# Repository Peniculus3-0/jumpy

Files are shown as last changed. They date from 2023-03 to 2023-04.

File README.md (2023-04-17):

# Jumpy

Jumpy est un robot sauteur réalisé dans le cadre du projet de session de la session 4 en Génie Robotique à l'Université de Sherbrooke. 

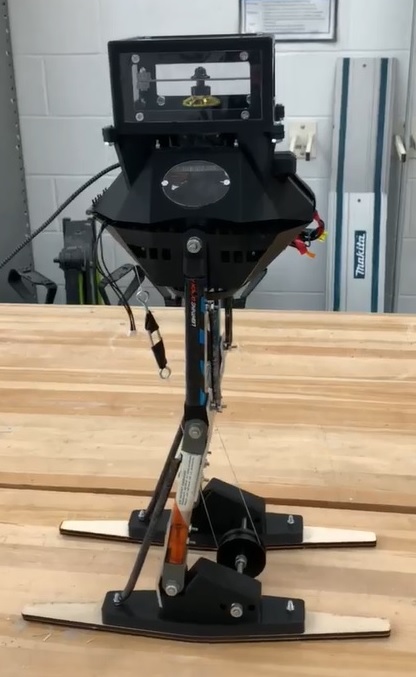
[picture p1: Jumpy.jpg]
JUMPY


## Table des matières

* [UI](/UI#requis)
* [Code contrôle](/Code/mainJumpy#code)
* [CAD](/CAD#CAD)

## VIDÉOS

[Démonstration du robot](https://www.youtube.com/shorts/cel7XVDD8pQ)

[Démonstration du saut à une jambe](https://www.youtube.com/shorts/icxFYxDteIQ)

[Démonstration de la roue inertielle](https://www.youtube.com/shorts/jROJLMc7-dI)

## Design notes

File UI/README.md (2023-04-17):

### Fonctionnalités

- Affichage de l'interface utilisateur avec un thème clair, sombre ou système.
- Recherche de dispositifs Bluetooth à proximité à l'aide du module bleak.
- Connexion à un dispositif Bluetooth sélectionné dans une liste déroulante.
- Animation du robot qui saute
- Lance le saut à distance par Bluetooth
- Affichage en temps réel de la vitesse et du couple actuels du moteur.

### Requis

1. Un ordinateur avec Python 3.x installé.
2. Un dispositif Bluetooth compatible pour contrôler le moteur.
3. Les modules Python suivants installés : customtkinter, PIL (Pillow), bleak, threading, os, logging, asyncio et turtle.
4. Lien vers les images des animations : https://drive.google.com/drive/folders/1fHX3-iR9xY-f3sybb7qTc169rCVtT3Wu?usp=sharing

  `pip install requirements.txt`
  
  ### Procédure
  
1. Assurez-vous que tous les prérequis sont satisfaits.
3. Exécutez le fichier UI.py pour lancer l'application.
4. L'application affichera l'interface utilisateur avec les options de recherche de dispositifs Bluetooth.
5. Sélectionnez un dispositif Bluetooth dans la liste déroulante et connectez-vous.

  ### Classe animation
  
- Affiche l'animation de repos et de saut du robot dans un frame custom Tkinter à une fréquence spécifié en bouclant les images en mémoire
- Charge les images dans des dictionnaires pour améliorer les performances

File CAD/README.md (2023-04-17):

# CAD
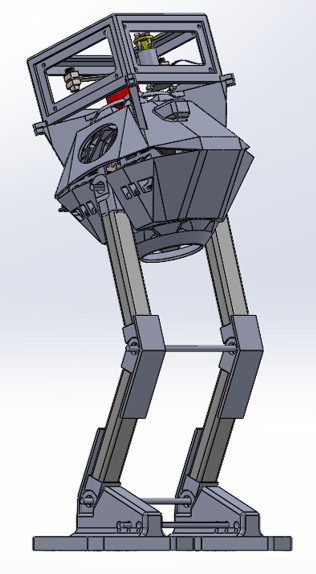
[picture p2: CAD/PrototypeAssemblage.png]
Assemblage

## REQUIS
* Une imprimante 3D
* Pour le reste des pièces, voir le [BOM](/BOM.pdf)

## PROCÉDURE

1. Imprimer les pièces 3D
2. Découper les plaques d'acrylique au laser
3. Découper et percer les plaques d'acier
4. Découper et plier les plaques d'aluminium
5. Couper les bâtons de hockey
6. Assembler les pièces imprimées et les bâtons

## ASSEMBLAGE DU ROBOT

### JAMBE

##### PIÈCES À IMPRIMER:
- Pied_V4_ECP (x2)
- Cheville_REV2_VF (x2)
- PoulieCheville_V1_CN (x1)
- JointDouble_REV0_AM (x6)

### BOITE DE CONTROLE

##### PIÈCES À IMPRIMER:
- AcrylicCage_V1_CN (x1)
- ControlBoxFrame_V2_CN (x1)
- TopFrame_V1_CN_InProgress (x1)
- GearMoteur_V5_ECP (x2)
- GearPulleyV1_LC (x1)
- Hinge_REV0_LC (x3)
- MotorHolder_V1_LCV (x1)

##### PLAQUES D'ACRYLIQUE À DÉCOUPER:
- AcrylicPlaqueSide1_V1_CN (x4)
- AcrylicPlaqueTop_V1_CN (x1)
- AcrylicWindowTopFrame_V1_CN (x1)

### ROUE INERTIELLE

##### PLAQUES D'ALUMINIUM À DÉCOUPER ET PLIER:
- Stopper20deg_REV0_CL (x2)
- Stopper40deg_REV0_CL (x2)

##### PLAQUES D'ACIER À DÉCOUPER ET PERCER
- PlaqueEpaisseFlywheel_CN_V2 (x4)
- PlaqueMinceFlywheel_CN_V2 (x1)

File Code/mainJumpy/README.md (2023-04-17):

# Code
## Installation OpenCR via le gestionnaire de cartes : 

1.	Une fois l'IDE Arduino exécuté, cliquez sur Fichier → Préférences dans le menu supérieur de l'IDE. Lorsque la fenêtre Préférences apparaît, copiez et collez le lien suivant dans la zone de texte URL supplémentaires du gestionnaire de cartes. (Cette étape peut prendre environ 20 minutes.)

https://raw.githubusercontent.com/ROBOTIS-GIT/OpenCR/master/arduino/opencr_release/package_opencr_index.json

2.	Cliquez sur Outils → Tableau → Gestionnaire de carte.
3.	Tapez OpenCR dans la zone de texte pour trouver le package OpenCR by ROBOTIS. Une fois trouvé, cliquez sur Installer.
4.	Après l'installation, "INSTALLÉ" apparaîtra.
5.	Vérifiez si la carte OpenCR est maintenant dans la liste Outils → Carte. Cliquez dessus pour importer la source de la carte OpenCR.

### Pour plus d’information :
https://emanual.robotis.com/docs/en/parts/controller/opencr10/#install-on-windows

## Installation des librairies :

1.	Cliquez sur Croquis → Inclure une bibliothèque → Gérer les bibliothèques.
2.	Tapez Dynamixel2Arduino dans la zone de texte pour trouver la bibliothèque by ROBOTIS. Une fois trouvé, cliquez sur Installer.
3.	Après l'installation, "INSTALLÉ" apparaîtra.

### Pour plus d’information :
https://docs.arduino.cc/software/ide-v1/tutorials/installing-libraries

## Utilisation du code Arduino :

Il n’y a que trois commandes possibles pour utiliser le code à partir du moniteur série :
-	« j » pour sauter sans tourner.
-	« l » pour sauter et tourner vers la gauche.
-	« r » pour sauter et tourner vers la droite. 
L’instruction « w » est juste un état qui ne fais rien en attendant la prochaine instruction.

Une fois qu’un saut est initié, il y a trois façons possibles de terminer une boucle de saut :
-	Le saut est détecté par une baisse soudaine de courant.
-	L’arrêt d’urgence est activé à cause d’un courant trop élevé
-	L’arrêt manuel est activé en envoyant n’importe quel caractère dans le moniteur série.

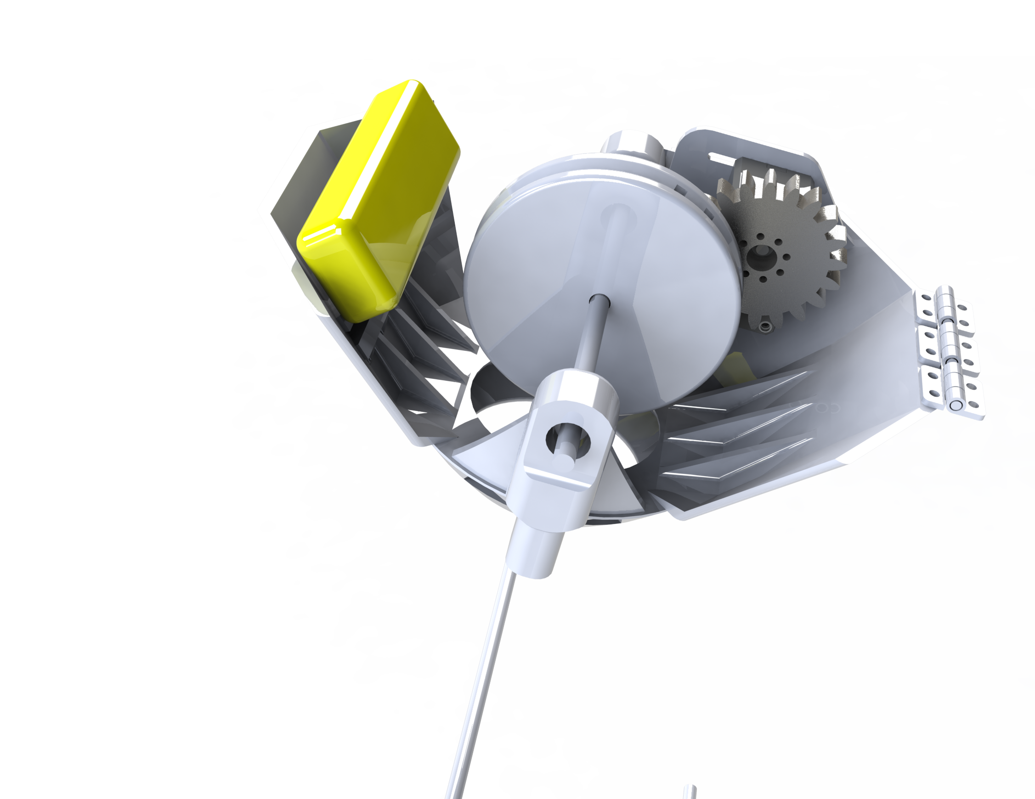
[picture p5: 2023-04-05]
UI/images/robot.png

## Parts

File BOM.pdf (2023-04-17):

Tableau 1 : Liste des pièces mécaniques du projet

Pièce | Description | Emplacement sur le
robot | Coût unitaire Fournisseur | Quantité | Coût total
1kg de PLA | - | - | 25 | FILAMENTS.CA | 1 | 25
Bâton de hockey | 20 cm | Jambes | 118.99 | Sports experts | 1 | 118.99
Ressorts | 800 N/m – 12 cm | Jambes | 5.95 | McMaster-Carr | 2 | 11.90
Ressorts | 800 N/m – 19 cm | Jambes | 5.95 | McMaster-Carr | 2 | 11.90
Roulements à bille | 10pcs Kozelo FR188ZZ Jambes | 19.49 | Amazon | 2 | 38.98
Arbre | ¼"φ – 20 cm | Jambes | 6.75 | McMaster-Carr | 3 | 19.50
Bague | 10pcs ¼"φ | Jambes | 18.74 | Amazon | 2 | 37.58
M3 boulons & noix | 100pcs – 20mm | Jambes & boîte contrôle | 4.99 | Amazon | 1 | 4.99
M4 boulons & noix | 100pcs – 20mm | Jambes & boîte contrôle | 4.99 | Amazon | 1 | 4.99
M5 boulons & noix | 100pcs – 20mm | Jambes & boîte contrôle | 4.99 | Amazon | 1 | 4.99
TOTAL | | | | | | 278.82

Tableau 2 : Liste des pièces électriques du projet

Grand total : 1300.14 CAD

Pièce | Description | Emplacement sur le
robot | Coût unitaire Fournisseur | Quantité | Coût total
Carte OpenCR | - | Boîte de contrôle supérieure 250 | Projet S4-GRO | 1 | 250
Dynamixel XM430 | - | Boîte de contrôle inférieure 300 | Projet S4-GRO | 2 | 600
Batterie Lithium | 3S – 25C | Boîte de contrôle inférieure 28.99 | AlieExpress | 1 | 28.99
Moteur BLDC | Scorpion M-3011-
760kv | Boîte de contrôle supérieure 89.99 | ScorpionSystem | 1 | 89.99
Contrôleur de vitesse ESC 25A | Boîte de contrôle supérieure 25.99 | ScorpionSystem | 1 | 25.99
Module bluetooth | DSD TECH HM-10 | Boîte de contrôle supérieure 14.39 | Amazon | 1 | 14.39
Fusible 5A | Fusible temporisé lent Boîte de contrôle supérieure 0.49 | Amazon | 1 | 0.49
Fusible 20A | Fusible temporisé lent Boîte de contrôle supérieure 0.49 | Amazon | 1 | 0.49
Fil | 18 AWG – 20 pieds | Boîte de contrôle | 10.98 | Amazon | 1 | 10.98
TOTAL | | | | | | 1021.32

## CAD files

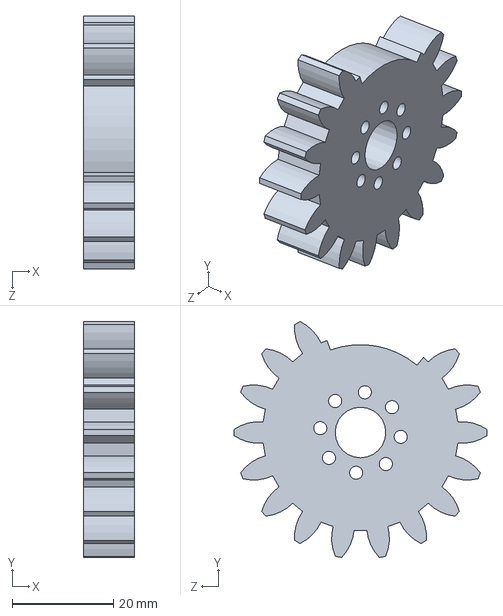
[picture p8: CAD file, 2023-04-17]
CAD/GearMoteur_V5_ECP.SLDASM
10.0 x 46.7 x 50.0 mm

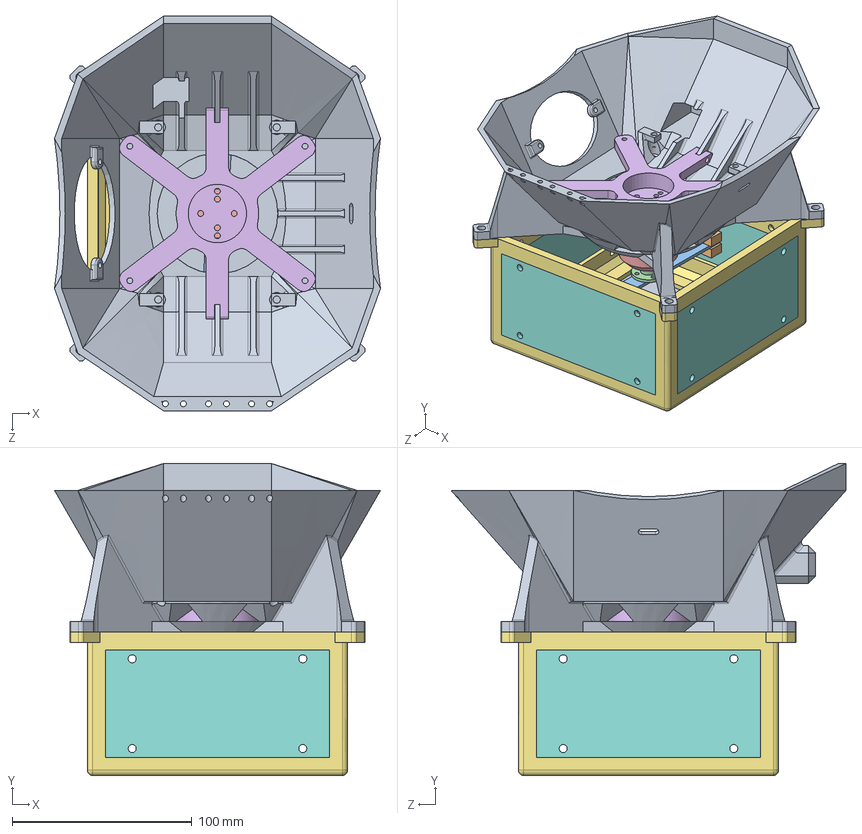
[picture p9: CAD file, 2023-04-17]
CAD/TopFrameWithFlywheel_V1_CN.SLDASM
181.6 x 173.8 x 220.0 mm
TopFrame_V1_CN_InProgress
PlaqueEpaisseFlywheel_CN_V2 x 4
PlaqueMinceFlywheel_CN_V2
FlywheelFlangeCoupling_V1_LC
FlywheelMotor_LCV_V2.smg
MotorHolder_V1_LCV
AcrylicCage_V1_CN
AcrylicPlaqueSide1_V1_CN x 4
AcrylicPlaqueTop_V1_CN

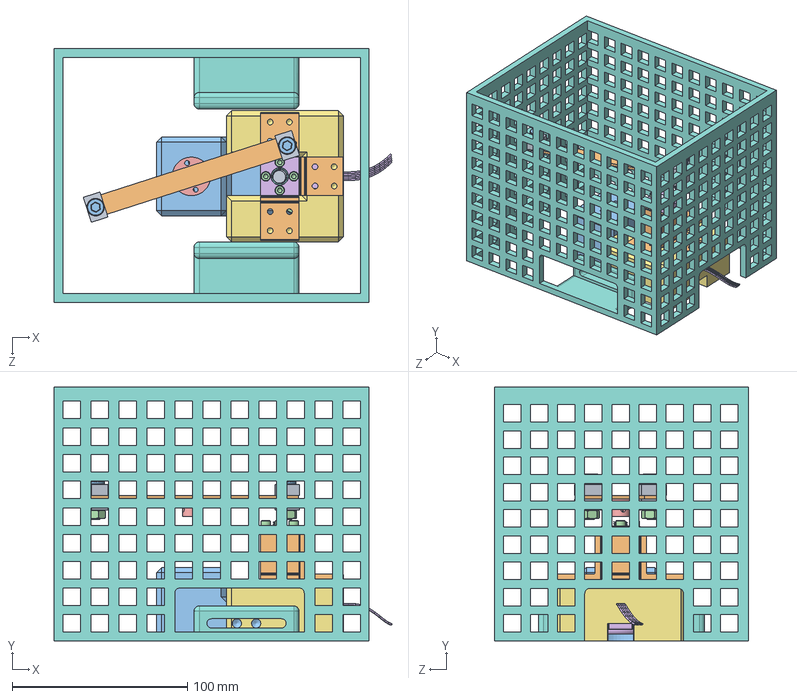
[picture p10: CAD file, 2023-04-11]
SherwoodUpToDate/FlywheelExternPrototype_V1_LC.SLDASM
193.1 x 145.0 x 145.0 mm
PlaqueEpaisseFlywheel_CN_V2 x 4
PlaqueMinceFlywheel_CN_V2
GB_1 x 2
M6 Hex nut x 2
FlywheelFlangeCoupling_V1_LC
Stepper motor 1PC.stp
LeadScrewMotorCoupler_V1_LC
LeadScrewNut_V1_LC
LeadScrew_V1_LC
AluminumSideBlocker_V1_LC x 3
FlywheelBrakePrototypeFrame_V1_LC
socket head cap screw_am x 6
hex nut style 1_am x 6
AluminumShaftStopper_V1_LC x 3
FlywheelTopFrame_V1_LC
CageFlywheel_V1_CN

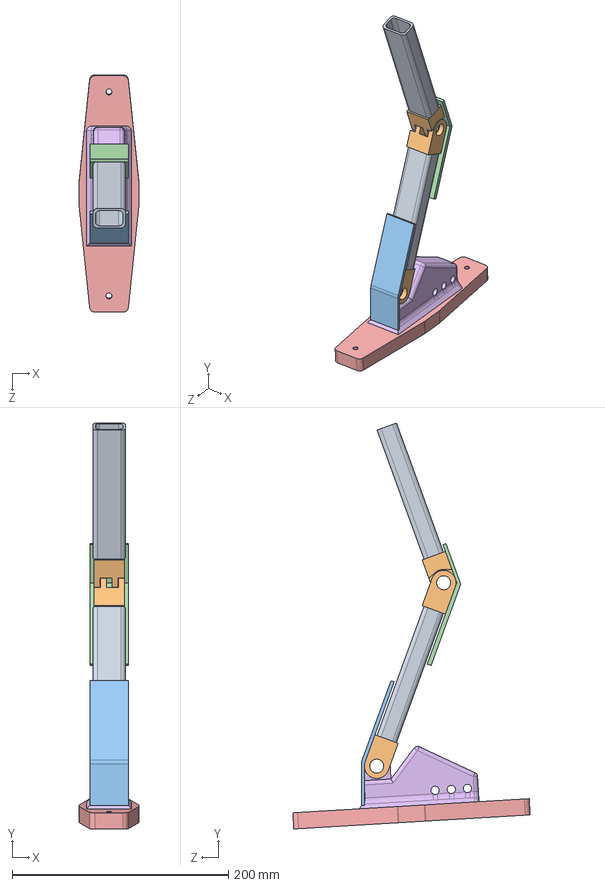
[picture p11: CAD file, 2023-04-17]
CAD/AssemblageJambe_REV3_CL.SLDASM
55.0 x 375.2 x 219.5 mm
Membre_REV0_CL x 2
JointDouble_REV0_AM x 3
Stopper20deg_REV0_CL
Stopper40deg_REV0_CL
Pied_V4_ECP.step
Cheville_REV2_VF

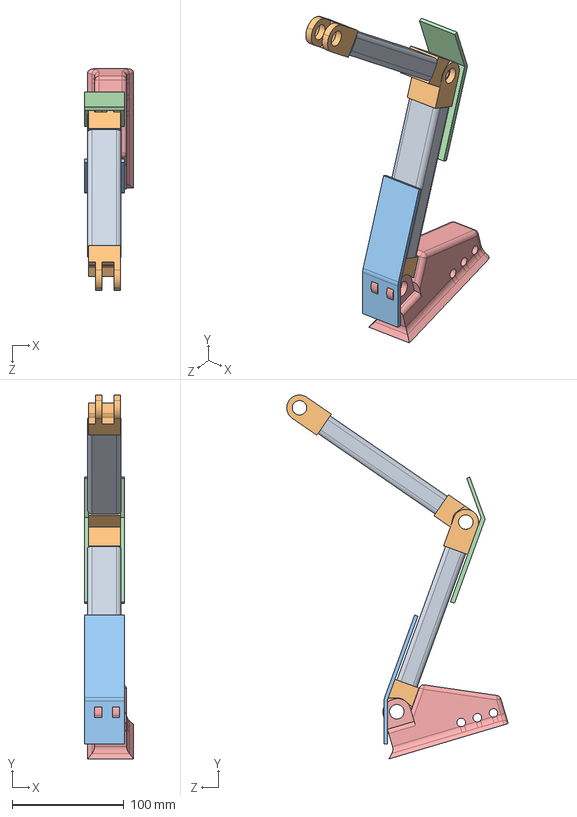
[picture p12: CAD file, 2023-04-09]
SherwoodUpToDate/AssemblageJambe_REV4_ECP.SLDASM
44.2 x 325.3 x 198.0 mm
Membre_REV0_CL x 2
JointDouble_REV0_AM x 4
Stopper20deg_REV0_CL
Stopper40deg_REV0_CL
Cheville_REV1_ECP

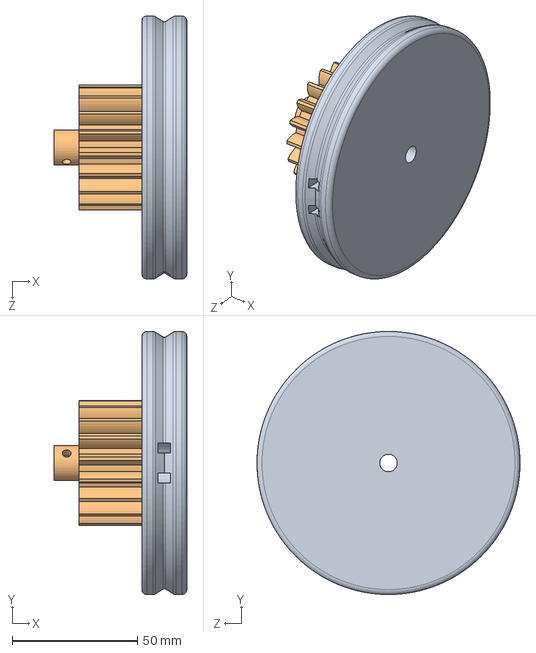
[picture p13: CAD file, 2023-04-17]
CAD/GearPulleyV1_LC.SLDASM
53.0 x 105.0 x 105.0 mm
NouvellePulleyModulaire
GearFil_V6_LC

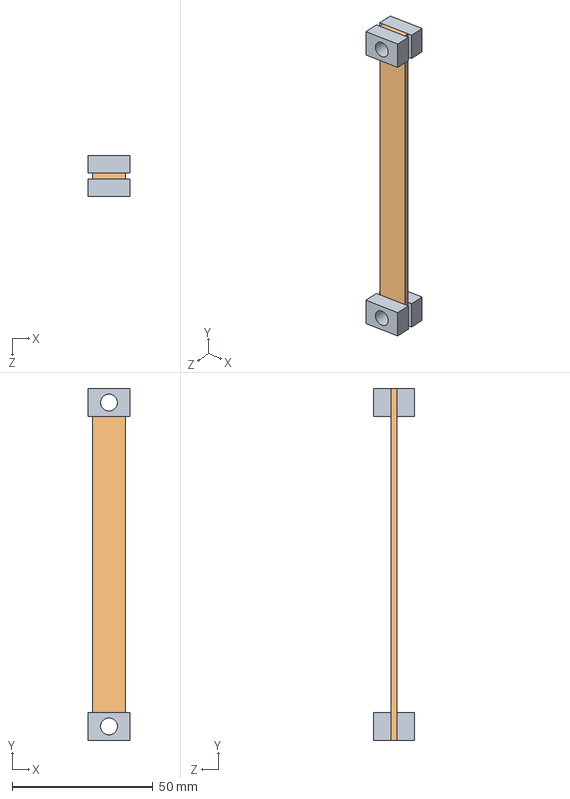
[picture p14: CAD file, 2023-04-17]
CAD/Flywheel_CN_V2.SLDASM
15.0 x 125.0 x 14.7 mm
PlaqueEpaisseFlywheel_CN_V2 x 4
PlaqueMinceFlywheel_CN_V2

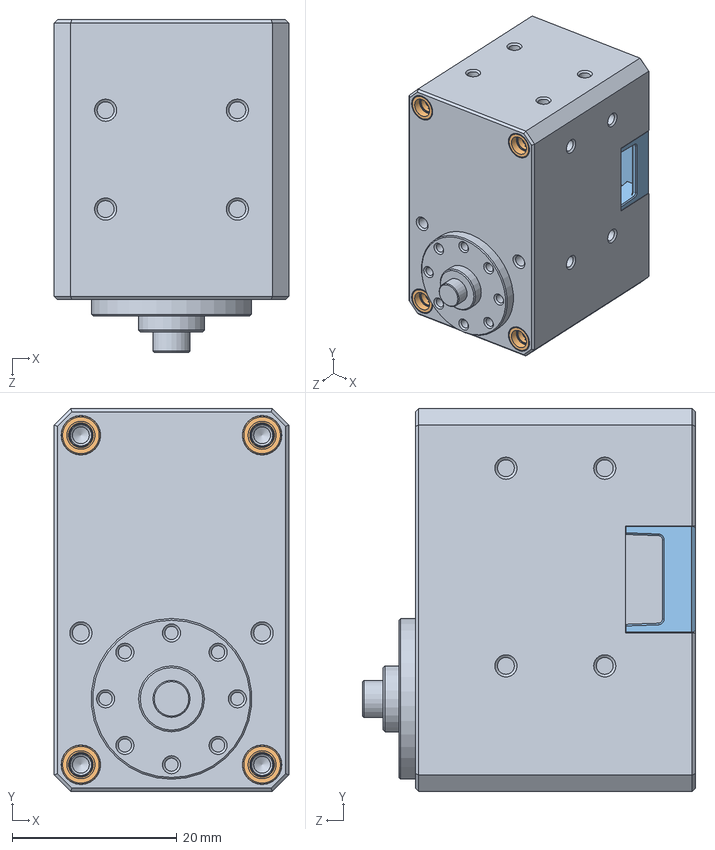
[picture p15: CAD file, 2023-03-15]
CAD/DXL-X430_REV0_LC.SLDASM
28.5 x 46.5 x 40.4 mm
DUMMY_DC12_STD.stp
DC12_A01_SPACER_RING.stp x 8
DC12_A01_CVR_CABLE.stp

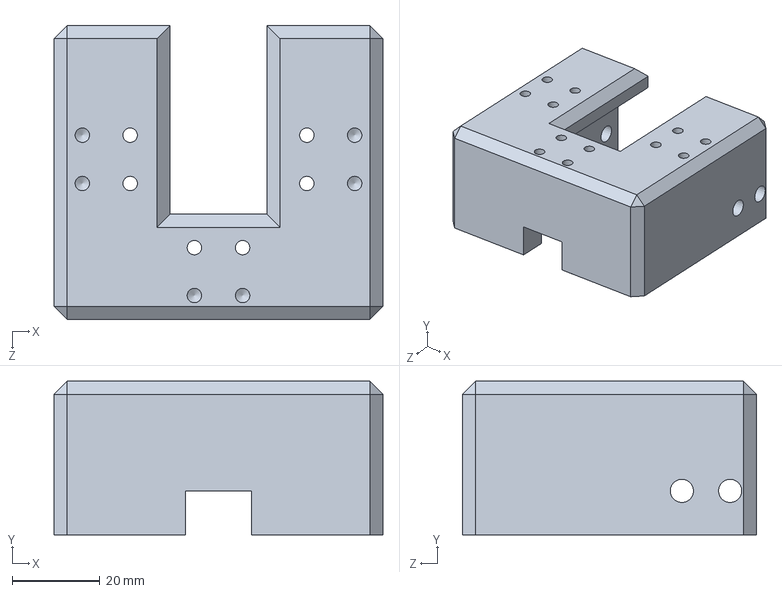
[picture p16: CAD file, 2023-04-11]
SherwoodUpToDate/FlywheelTopFrame_V1_LC.SLDPRT
75.0 x 35.0 x 67.0 mm

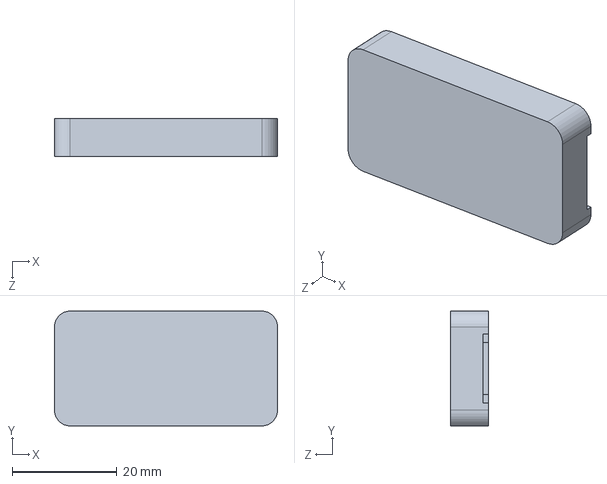
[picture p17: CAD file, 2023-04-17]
CAD/ModuleBluetooth_V1_CN.SLDPRT
42.6 x 22.0 x 7.20 mm

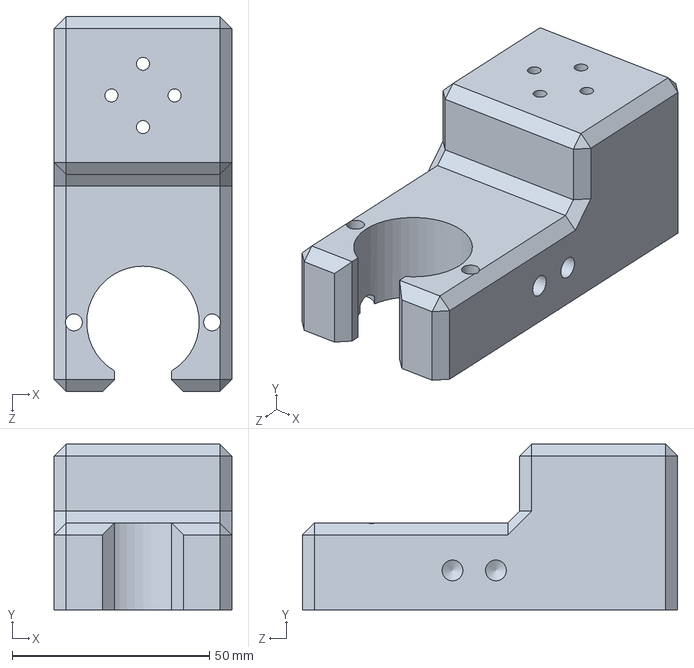
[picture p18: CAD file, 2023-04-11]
SherwoodUpToDate/FlywheelBrakePrototypeFrame_V1_LC.SLDPRT
45.0 x 42.0 x 95.0 mm

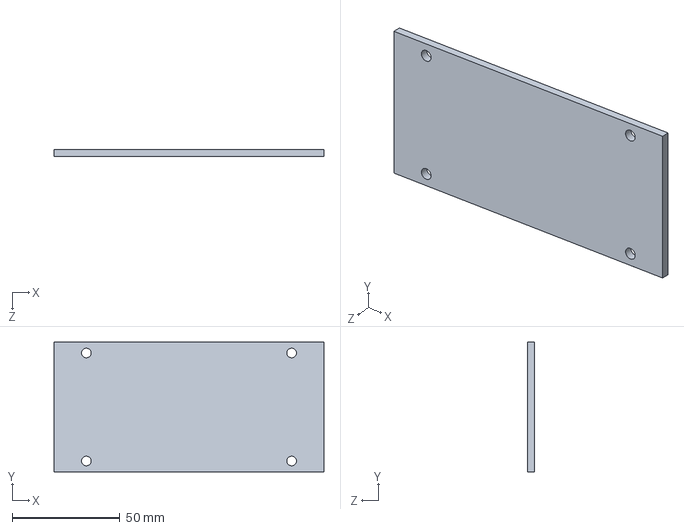
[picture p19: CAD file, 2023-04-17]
CAD/AcrylicPlaqueSide1_V1_CN.SLDPRT
125.0 x 60.0 x 3.17 mm

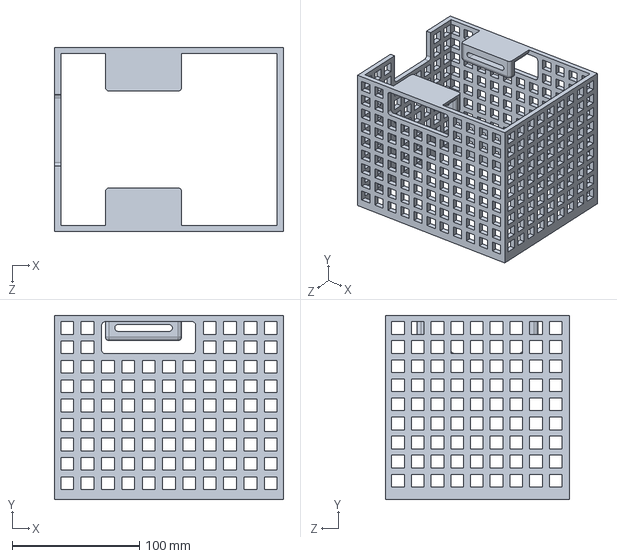
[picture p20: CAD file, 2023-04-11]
SherwoodUpToDate/CageFlywheel_V1_CN.SLDPRT
180.0 x 145.0 x 145.0 mm

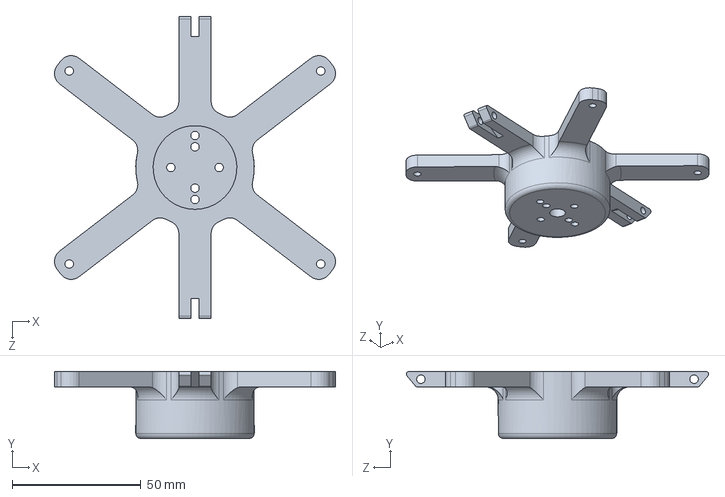
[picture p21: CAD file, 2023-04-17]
CAD/MotorHolder_V1_LCV.SLDPRT
109.0 x 26.0 x 117.3 mm

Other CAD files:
CAD/OpenCR_REV0_LC.step.SLDASM
SherwoodUpToDate/AluminumSideBlocker_V1_LC.SLDPRT
CAD/TopFrame_V1_CN_InProgress.SLDPRT
CAD/AcrylicWindowTopFrame_V1_CN.SLDPRT
CAD/022035025.step.SLDPRT
CAD/530470210.step.SLDPRT
CAD/AcrylicCage_V1_CN.SLDPRT
CAD/AcrylicPlaqueTop_V1_CN.SLDPRT
CAD/Battery_REV0_CL.SLDPRT
CAD/CP_Elec_10x10.step.SLDPRT
CAD/CP_Elec_5x53.step.SLDPRT
CAD/CP_Elec_8x10.step.SLDPRT
CAD/CUI_PJ-102A-18.step.SLDPRT
CAD/CUI_PJ-102A-21.step.SLDPRT
CAD/CUI_PJ-102A-7.step.SLDPRT
CAD/CUI_PJ-102A.step.SLDPRT
CAD/Cheville_REV2_VF.SLDPRT
CAD/ControlBoxFrame_V2_CN.SLDPRT
CAD/FlywheelFlangeCoupling_V1_LC.SLDPRT
CAD/FlywheelMotor_LCV_V2.smg.SLDPRT
CAD/GearFil_V6_LC.SLDPRT
CAD/HTSSOP_28_1EP_44x97mm_P065mm.step.SLDPRT
CAD/Hinge_REV0_LC.SLDPRT
CAD/JST_B3B_EH_A.step.SLDPRT
CAD/JST_B4B_EH_A.step.SLDPRT
CAD/JointDouble_REV0_AM.SLDPRT
CAD/LED_0603_1608Metric.step.SLDPRT
CAD/LM1117.step.SLDPRT
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

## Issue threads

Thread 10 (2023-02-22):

Bluetooth

loiccv123, 2023-02-22:

Anto39, 2023-03-04:
- Connecter le hc-06 au arduino mega
- Runner de examples
- Le hc-06 ne fonctionne pas avec un Iphone le protocole Bluetooth n'est pas le même
- Test envoie de commande avec l'ordinateur

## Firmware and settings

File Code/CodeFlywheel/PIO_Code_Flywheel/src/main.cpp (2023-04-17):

#include <Arduino.h>
#include <Servo.h>
#include <U8g2lib.h>
#include <Wire.h>
#include <Stepper.h>

#define STEPS 32
#define REDUCTION_RATIO 64
#define STEPS_PER_REVOLUTION (STEPS * REDUCTION_RATIO)

Servo ESC;
U8G2_SSD1306_64X32_1F_F_HW_I2C u8g2(U8G2_R0, /* reset=*/ U8X8_PIN_NONE);
Stepper stepper(STEPS, 8, 10, 9, 11);
int potValue;

void PrintScreen(int potValue, int steps);

void setup() {
      Serial.begin(9600);
      ESC.attach(3, 1000, 2000);
      u8g2.begin();
      u8g2.setFont(u8g2_font_profont12_tf);
}

void loop()
{
      potValue = analogRead(A1);
      potValue = map(potValue, 0, 1023, 0, 180);
      
      int steps;
      int totalSteps;

      stepper.setSpeed(300);
      stepper.step(-10000);


      // if (Serial.available() > 0) {
      //       steps = Serial.parseInt();
      //       stepper.step(steps);
      // }
      ESC.write(potValue);

      PrintScreen(potValue, totalSteps += steps);
      // delay(100);
}

void PrintScreen(int potValue, int steps)
{
      u8g2.clearBuffer();
      char buf_stp[20];
      sprintf(buf_stp, "STP : %d", steps);
      u8g2.setCursor(10, 20);
      u8g2.print(buf_stp);

      u8g2.setCursor(10, 30);
      char buf_pot[20];
      sprintf(buf_pot, "POT : %d", potValue);
      u8g2.print(buf_pot);      
      u8g2.sendBuffer();
}

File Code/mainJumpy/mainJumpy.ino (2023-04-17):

#include "ControleDynamixel.h"
#include "ControleFlywheel.h"
#include "Bluetooth.h"

const int PERIODE_BLUETOOTH = 10;  //ms
const int RMP_FLYWHEEL = 80; //Vitesse de la flywheel
const int RMP_JUMP = 6;

volatile char instruction;
volatile int RPM_flywheel_bluetooth = RMP_FLYWHEEL;
volatile int RPM_jump_bluetooth = RMP_JUMP;
volatile float CourrantM1_bluetooth = 0;

  

//Timer pour l'interruption
HardwareTimer Timer(TIMER_CH1);

void setup() {
  setupBluetooth();
  setupControleDynamixel();
  setupControleFlywheel();
  Timer.stop();
  Timer.setPeriod(PERIODE_BLUETOOTH * 1000);  //Timer utilise des microsecondes
  Timer.attachInterrupt(readBluetooth);
  Timer.start();
  turn(0);
}

void loop() {
  if (Serial.available())  //Choisir "No Line Ending" dans Serial Monitor
  {
    instruction = Serial.read();
  }

  /* Instrction pour le switch case
   j : sauter
   l : tourner à gauche
   r : tourner à droite
   w : attente
  */
  switch (instruction) {
    case 'j':
      jump(RMP_JUMP);
      instruction = 'w';
      break;

    case 'l':
      jump(RMP_JUMP);
      turn(RMP_FLYWHEEL);
        instruction = 'w';
      break;

    case 'r':
      jump(RMP_JUMP);
      turn(RMP_FLYWHEEL);
        instruction = 'w';
      break;
  }
}

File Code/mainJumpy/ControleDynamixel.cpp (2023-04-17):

#include "actuator.h"
#include "Dynamixel2Arduino.h"
#include "ControleDynamixel.h"

#if defined(ARDUINO_OpenCR)  // Pour les cartes officiel ROBOTIS avec circuit DXL.
// Pour le OpenCR, il y a une pin "DXL Power Enable" qui doit être initialisé et contrôlé
// Reference : https://github.com/ROBOTIS-GIT/OpenCR/blob/master/arduino/opencr_arduino/opencr/libraries/DynamixelSDK/src/dynamixel_sdk/port_handler_arduino.cpp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
#define DXL_SERIAL Serial3
#define DEBUG_SERIAL Serial
const int DXL_DIR_PIN = 84;  // OpenCR DIR PIN.
#endif


const uint8_t DXL_ID1 = 17;
const uint8_t DXL_ID2 = 1;
const float DXL_PROTOCOL_VERSION = 2.0;
const float RANGE_DETECTION_LOAD = 100;
const int MAX_SAFETY_CURRENT = 650;
extern volatile float CourrantM1_bluetooth;

Dynamixel2Arduino dxl(DXL_SERIAL, DXL_DIR_PIN);

//Requis pour contrôler la "control table"
using namespace ControlTableItem;


void setupControleDynamixel() {
  // Utilise port UART du DYNAMIXEL Shield pour debug.
  DEBUG_SERIAL.begin(115200);

  // Définis le baudrate à 57600bps. Cela doit être pareil que le baudrate du DYNAMIXEl.
  dxl.begin(57600);
  // Définis la version du protocole. Cela doit être pareil que la version de protocole du DYNAMIXEL.
  dxl.setPortProtocolVersion(DXL_PROTOCOL_VERSION);
  // Reçois les informations du DYNAMIXEL 
  dxl.ping(DXL_ID1);
  dxl.ping(DXL_ID2);

  // Désactivation du torque lors de la configuaration dans le EEPROM
  dxl.torqueOff(DXL_ID1);
  dxl.setOperatingMode(DXL_ID1, OP_VELOCITY);
  dxl.torqueOn(DXL_ID1);

  dxl.torqueOff(DXL_ID2);
  dxl.setOperatingMode(DXL_ID2, OP_VELOCITY);
  dxl.torqueOn(DXL_ID2);
}

//INPUT : RPM [-10/10]
//OUTPUT : Bool return 0 si pas d'erreur
bool jump(float RPMGOAL) {

  dxl.torqueOn(DXL_ID1);
  dxl.torqueOn(DXL_ID2);

  dxl.setGoalVelocity(DXL_ID1, RPMGOAL, UNIT_RPM);
  dxl.setGoalVelocity(DXL_ID2, RPMGOAL, UNIT_RPM);

  float actualLoad = (dxl.getPresentCurrent(DXL_ID1));
  float lastLoad = actualLoad;

  DEBUG_SERIAL.println(dxl.getPresentCurrent(DXL_ID1));
  DEBUG_SERIAL.println(dxl.getPresentCurrent(DXL_ID2));
  float currentdx1 = 0;
  float currentdx2 = 0;

  /*Cette boucle permet de détecté si il y a un front déscendant de courant
    dans les moteurs signifiant qu'il y a eu un saut, ainsi d'arrêter le robot */
  while ((actualLoad + RANGE_DETECTION_LOAD) > lastLoad) {

    currentdx1 = dxl.getPresentCurrent(DXL_ID1);
    currentdx2 = dxl.getPresentCurrent(DXL_ID2);
    CourrantM1_bluetooth = currentdx1;    

    Serial.print(currentdx1);
    Serial.print("\t");
    Serial.print(currentdx2);
    Serial.print("\t");
    Serial.print(currentdx2 - currentdx1);
    Serial.print("\t");
    Serial.println(abs(currentdx2) + abs(currentdx1));
    
    //Arrêt d'urgence si le torque devient trop élevé pour pas brisé le robot
    if ((abs(currentdx1) + abs(currentdx2)) >= MAX_SAFETY_CURRENT) {
      dxl.setGoalVelocity(DXL_ID1, 0);
      dxl.setGoalVelocity(DXL_ID2, 0);
      dxl.torqueOff(DXL_ID1);
      dxl.torqueOff(DXL_ID2);
      Serial.println("Safety engaged");
      return 1;
    }
    //Arrêt manuel si l'on souhaite arrêter le robot lors d'un saut
    if (Serial.available()) {
      Serial.read();
      dxl.setGoalVelocity(DXL_ID1, 0);
      dxl.setGoalVelocity(DXL_ID2, 0);
      dxl.torqueOff(DXL_ID1);
      dxl.torqueOff(DXL_ID2);
      Serial.println("stop");
      return 0;
    }
    lastLoad = actualLoad;
    actualLoad = currentdx1;
  }

  Serial.print(currentdx1);
  Serial.print("\t");
  Serial.print(currentdx2);
  Serial.print("\t");
  Serial.print(currentdx2 - currentdx1);
  Serial.print("\t");
  Serial.println(abs(currentdx2) + abs(currentdx1));

  Serial.println("Drop detected");
  dxl.setGoalVelocity(DXL_ID1, 0);
  dxl.setGoalVelocity(DXL_ID2, 0);
  return 0;
}

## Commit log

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2023-02-16 Update Cad Chris, ajout de poulie cremaillere
    [Bottom_leg.SLDPRT, Jumpy_assembly.SLDASM, Knee - Copy.SLDPRT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]
2023-02-18 Sherwood
    Add folder with chosen prototype named sherwood parts and assembly up to date
    [BaseRobotSauteurRecent.sldprt, Bâton.SLDPRT, HockeyPrototypeJoinRecent.sldprt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]
2023-02-19 Sherwood
    Update to foot and kneecap design
    [BaseRobotSauteurRecent.sldprt, Leg_assembly.SLDASM, kneecap.SLDPRT]
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2023-02-22 Update of Sherwood CADs
    [BaseRobotSauteurRecent (1).sldprt, BaseRobotSauteurRecent.sldprt, Boite_controle.sldprt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]
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2023-02-22 Fixed push error
    [BaseRobotSauteur.sldprt]
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2023-03-04 Updated gear_motor and assembly
    [Gear_shaft.sldprt, gear_motor.sldprt, gear_motor_v2.SLDPRT]
2023-03-10 Updated Control box CAD, NEW ASSEMBLY : BOITE DE CONTROLE/NEW CHEST FRAME
    [20x20 3D Print Hinge.step.SLDPRT, Back_ChestPlate4.SLDPRT, Back_ChestPlate_final.SLDPRT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]
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2023-03-10 Add joint simple plus solide
    [Jointsimple.SLDPRT]
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2023-03-10 Calcul centre de masse sur new_chest_frame assembly
    [Front_ChestPlate4.SLDPRT, Gear.SLDPRT, batterie.SLDPRT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]
2023-03-10 New feet (with plexiglass plate) and midway through new contol box
    [BaseRobotSauteurV3.SLDPRT, BaseRobotSauteur_plexiglass.SLDPRT, Boite_controle_facing_downwards.SLDPRT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]
2023-03-11 boite de controle à finir par charles
    [Boite_controle_facing_downwards.SLDPRT, Boite_de_controle à finir par charles.SLDASM, Side_panel_plexiglass.SLDPRT]
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2023-03-13 Complete renaming and reorganisation of git files
    [20x20 3D Print Hinge.step.SLDPRT, AssemblageJambe_REV3_CL.SLDASM, Back_ChestPlate4.SLDPRT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]
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2023-03-14 Some modifications to control box, more to come soon
    [Boite_controle_facing_downwards.SLDPRT, Boite_de_controle à finir par charles.SLDASM, Clip_Assembly_V1_LCV.SLDASM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]
2023-03-14 some file changes i guess
    [20x20 3D Print Hinge.step.SLDPRT, AssemblageJambe_REV3_CL.SLDASM, Back_ChestPlate4.SLDPRT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]
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2023-03-14 t'es tu content charles
    [ControlBoxFrame_REV3_LC.SLDPRT, GearFil_V4_CN.SLDPRT, GearMoteur_V3_CN.SLDPRT]
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2023-03-15 V1 du top frame et modifications du bottom frame
    [ControlBoxFrame_REV3_LC.SLDPRT, DXL-X430_REV0_LC.SLDASM, InnerBuckleV1_LCV.SLDPRT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]
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2023-03-15 Modifications boîte contrôle inférieure
    [ControlBoxFrame_REV3_LC.SLDPRT]
2023-03-16 Sherwood assembly, cad module bluetooth, TopPart boîte de contrôle
    [022035025.step.SLDPRT, 530470210.step.SLDPRT, CP_Elec_10x10.step.SLDPRT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]
2023-03-20 Frame top part, assembly advanced
    [FlywheelMotor_REV0_LC.SLDPRT, Flywheel_v1_Antoine.SLDASM, PartAluFlywheel_v1_Antoine.SLDPRT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]
2023-03-20 Battery holder reposition in bottom control box, small adjustment in top control box
    [ControlBoxFrame_REV3_LC.SLDPRT, TopFrame_V1_CN_InProgress.SLDPRT]
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2023-03-21 masse500g for flywheel motor model, top frame and assembly updated
    [Flywheel_v1_Antoine.SLDASM, PlexiglassWindow_CN_V1.SLDPRT, TopFrame_V1_CN_InProgress.SLDPRT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]
2023-03-23 CalculFLywheel, modification cad flywheel, boite de controle et assemblage
    [Flywheel_CN_V2.SLDASM, Flywheel_v1_Antoine.SLDASM, GB_1.SLDPRT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]
2023-03-26 Added motor holder part v1
    [Flywheel_CN_V2.SLDASM, MotorHolder_V1_LCV.SLDPRT, TopFrame_V1_CN_InProgress.SLDPRT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]
2023-03-27 MotorHolder adapted, top frame and assembly
    [MotorHolder_V1_LCV.SLDPRT, TopFrame_V1_CN_InProgress.SLDPRT]
2023-03-27 Modified motor part holder and added new bldc flywheel motor
    [FlywheelFlangeCoupling_V1_LC.SLDPRT, FlywheelMotor_LCV_V2.smg.SLDPRT, MotorHolder_V1_LCV.SLDPRT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]
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2023-03-30 New gear and pully, and started modifying the motor position in the lower control box
    [AssemblageJambe_REV3_CL.SLDASM, ControlBoxFrame_REV3_LC.SLDPRT, FuckallModulaireNewGear_V1_LC.SLDASM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]
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2023-03-30 Added new gear and pulley because of missing parts
    [FuckallModulaireNewGear_V1_LC.SLDASM, GearFil_V5_CN.SLDPRT, GearFil_V6_LC.SLDPRT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]
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2023-03-31 Boîte de contrôle prête à être imprimée, assemblage
    [AssemblageJambe_REV3_CL.SLDASM, ControlBoxFrame_V2_CN.SLDPRT]
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2023-03-31 Update to Bottom control box (Newly printed version)
    [AssemblageJambe_REV3_CL.SLDASM, ControlBoxFrame_V2_CN.SLDPRT, Flywheel_CN_V2.SLDASM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]
2023-04-02 Modifications aux hinges de la boîte de contrôle. Charles fix dont l'assembly tout peté svp
    [ControlBoxFrame_V2_CN.SLDPRT, TopFrame_V1_CN_InProgress.SLDPRT]
2023-04-02 Up to date control box (printed version with less supports)
    [ControlBoxFrame_V2_CN.SLDPRT]
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2023-04-05 Revert "A bit of cleanup of old files"
    This reverts commit b84818fb5d1f80c9fda469e5de8e4e99e80f947b.
    [AssemblageJambe_REV3_CL.SLDASM, Cheville_REV0_LC.SLDPRT, Cheville_V3_CN.SLDPRT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]
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2023-04-05 deleted old version of control box to fix pull issue
    [ControlBoxFrame_REV3_LC.SLDPRT]
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2023-04-05 Modification of motor holder and duplication to add another motor
    [ControlBoxFrame_V2_CN.SLDPRT]
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2023-04-06 Ajout trous pour fixer fil de pêche
    [ControlBoxFrame_V2_CN.SLDPRT]
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2023-04-06 Revert "update to animation and ui"
    This reverts commit 1b19bbf9a7d92c65c12be39a5bb0b0322084d4c1.
    [pyvenv.cfg]
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2023-04-08 modif code pour bluetooth avec varibale global + modifs chevilles
    [AssemblageJambe_REV4_ECP.SLDASM, Cheville_REV1_ECP.SLDPRT, Cheville_REV2_VF.SLDPRT]
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2023-04-10 final update to first flywheel prototype (printed version)
    [FlywheelBrakePrototypeFrame_V1_LC.SLDPRT, FlywheelExternPrototype_V1_LC.SLDASM, FlywheelTopFrame_V1_LC.SLDPRT]
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2023-04-11 AcrylicCage for flywheel, topframe to fix flywheel
    [AcrylicCage_V1_CN.SLDPRT, CageFlywheel_V1_CN.SLDPRT, TopFrame_V1_CN_InProgress.SLDPRT]
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2023-04-12 Quick modifications sur la top frame de charles (Version finale du print)
    [TopFrame_V1_CN_InProgress.SLDPRT]
2023-04-12 motorHolder ready to print, cage holes need to be modified
    [AcrylicCage_V1_CN.SLDPRT, Flywheel_CN_V2.SLDASM, MotorHolder_V1_LCV.SLDPRT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]
2023-04-13 Quick modifs version finales flywheel motor holder & cage
    [AcrylicCage_V1_CN.SLDPRT, MotorHolder_V1_LCV.SLDPRT, TopFrameWithFlywheel_V1_CN.SLDASM]
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
